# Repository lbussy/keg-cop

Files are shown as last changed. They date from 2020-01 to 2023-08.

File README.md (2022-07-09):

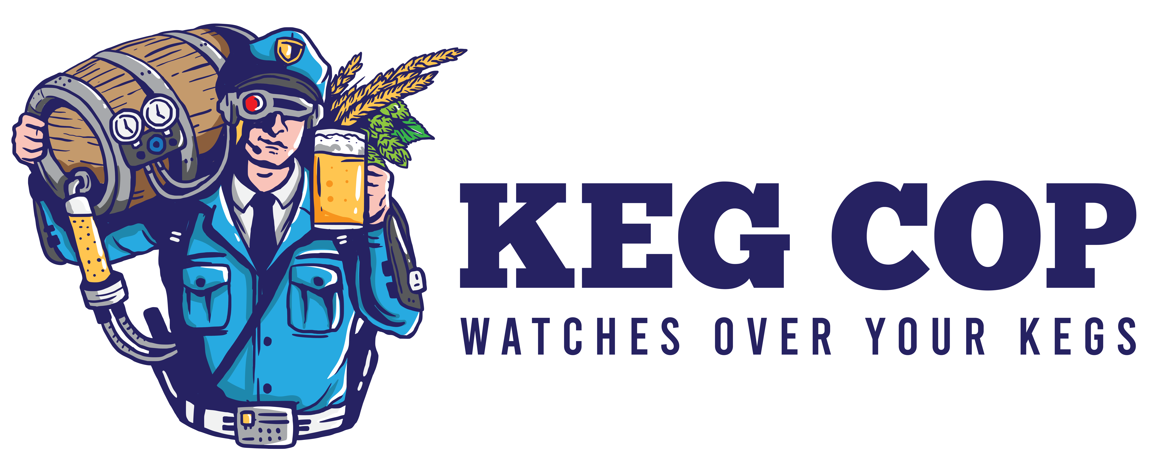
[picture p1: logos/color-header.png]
Keg Cop Logo
 

# Keg Cop

*Beverage Lines, Monitored.*

Keg Cop is an inexpensive and, most of all, simple to operate WiFi-enabled solution to maintain information about your Keezer, Kegerator, and Kegs.  Keg Cop enables you to use flowmeters of your choice (Swissflow during development) to monitor the contents of your kegs, and it even has a built-in Web UI to display what is on tap and how much is left.

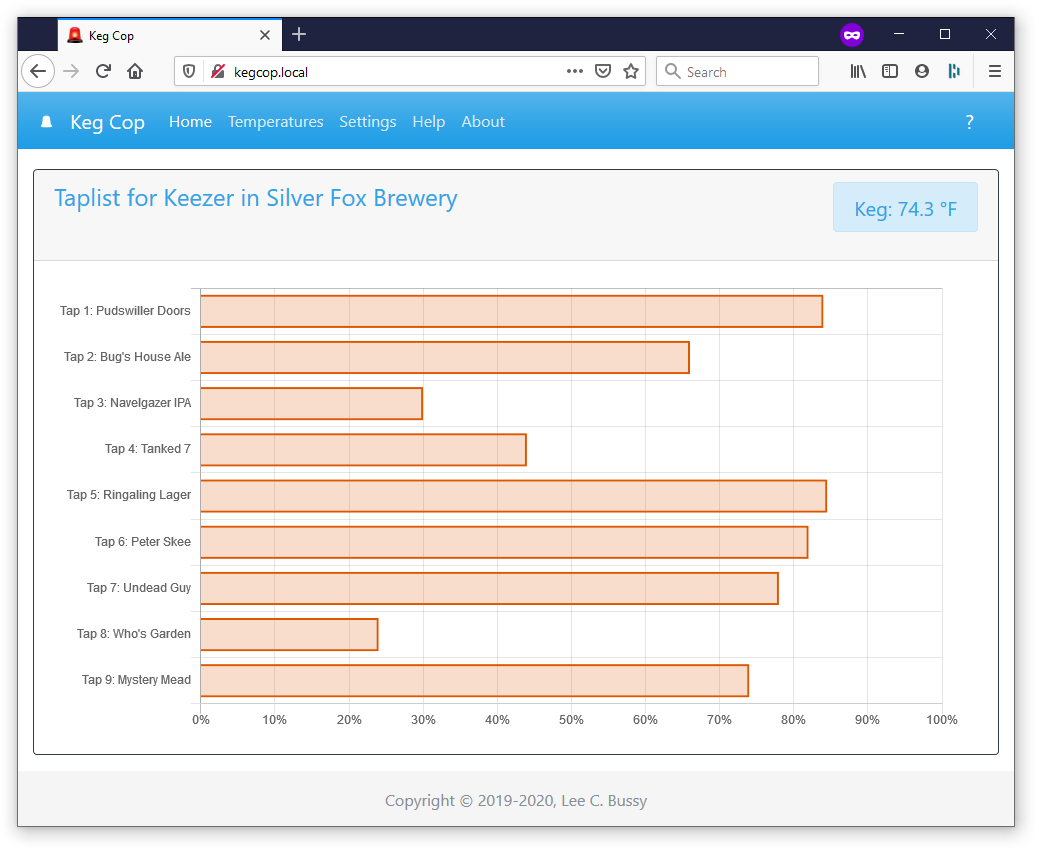
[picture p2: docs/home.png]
Keg Cop Index

 
Keg Cop uses an inexpensive ESP32 controller to control and monitor all aspects of your beverage dispensing solution.  If you already have flowmeters from another project, you can easily use those and upgrade your approach.  It will support one to nine flowmeters, and it will even control your temperatures for you.

You may employ up to five different temperature sensors to show you things like tower temp, keg temp, top and bottom of your Keezer, and you can even monitor the room temperature.

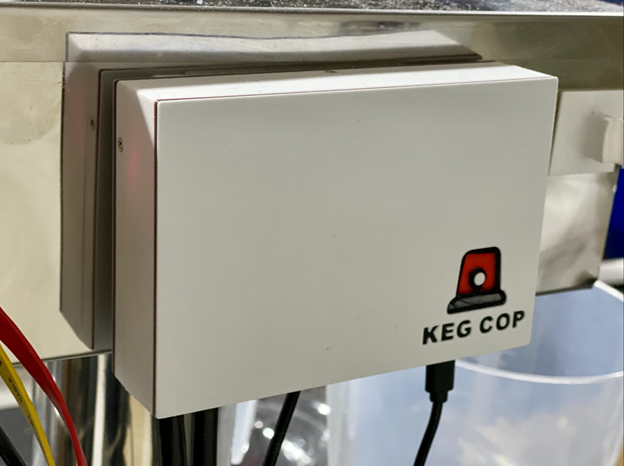
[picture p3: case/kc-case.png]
Keg Cop Case

 
I designed this project as a complete system from the ground up.  Everything is provided, including board files for PCBs and 3D models for cases.  I’m releasing this system as something which provides either a complete recipe for success or enough information to allow you to roll your own if that’s your thing.

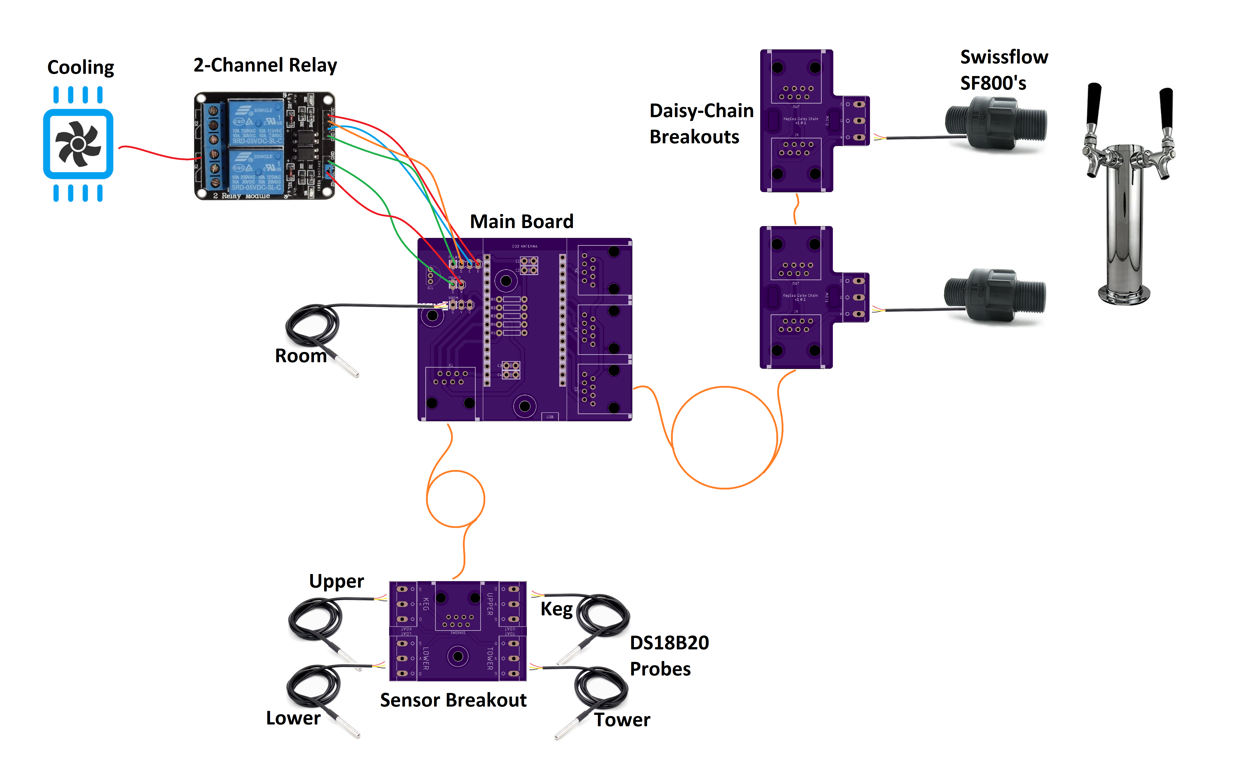
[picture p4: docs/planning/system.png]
Keg Cop System


Whether you have one flowmeter or nine, Keg Cop can handle them.  Have more?  Add another controller, and KegScreen (coming soon!) will seamlessly display them all.

Want even more capabilities?  Keg Cop will report pours to Raspberry Pints via MQTT or a web endpoint with a generic JSON packet.
Still not enough?  Keg Cop was designed alongside KegScreen to work hand in hand with this exciting upcoming full-featured tap list solution.

Full documentation is provided, including the API and hardware assembly.  Or, if you are a more nuts and bolts person, GitHub may be the place for you!

Links and Support:

-	Home Page
-	Project on GitHub
-	Documentation
-	Report an Issue or Bug
-	Get support or chat with other users

This release has been a long time coming, and I’m excited to share this with you.  I want to thank the following folks from Homebrewtalk who have contributed in one way or another:

-	@thorrak
-	@gromitdj
-	@UncleD
-	@day_trippr
-	@cripplecreek

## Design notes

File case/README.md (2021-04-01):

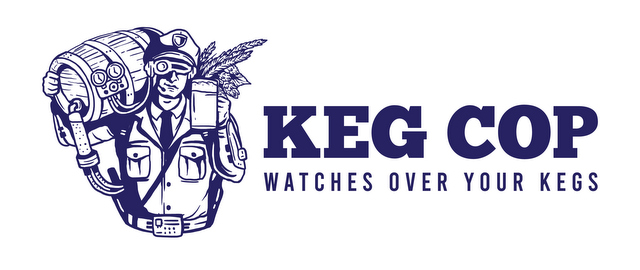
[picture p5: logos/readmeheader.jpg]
Keg Cop Logo Keg Cop (http://www.kegcop.com/)


# 3D Printed Cases

Within these folders are 3D models of cases which you may use in your own deployments:

- **Main Boards:**  Contains the top and bottom case halves for the main board.  These have been tested in PLA and PETG.  Additionally, there is a color-print enabled logo in the lid should you choose to take advantage of it.  I recommend the following layers:
    - 0.15mm layers
        - 0.00 - 0.65: Main body color (I used white)
        - 0.80 - 1.25: Dark border color (I used black)
        - 1.40 - 1.85: Base color (I used silver)
        - 2.00 - 2.60: Globe color (I used translucent red)
    - 0.20mm layers
        - 0.00 - 0.60: Main body color (I used white)
        - 0.80 - 1.20: Dark border color (I used black)
        - 1.40 - 1.80: Base color (I used silver)
        - 2.00 - 2.60: Globe color (I used translucent red)

Layer Configuration

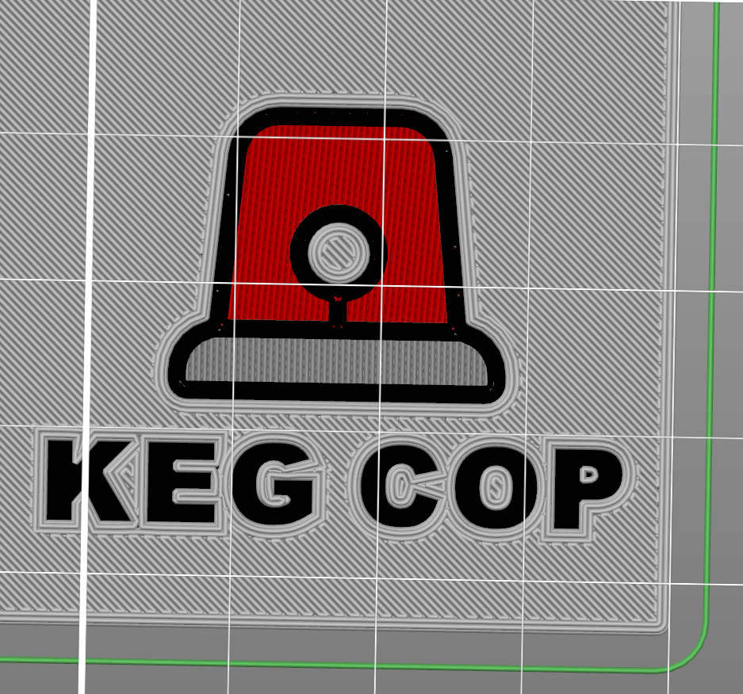
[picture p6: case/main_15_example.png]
Layer Render


- **Breakouts:**
    - Daisy Chain:
    - Temp Sensor:

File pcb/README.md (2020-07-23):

Keg Cop Logo Keg Cop (http://www.kegcop.com/)

# Printed Circuit Boards for Keg Cop

Contained here are two folders:

- **Main Boards:** Boards which receive the D32 controller, and provide connectivity to the breakouts.
- **Breakouts:** Boards which distribute and receive signals within the kegerator/keezer.

The type and number required of each board will vary by the intended configuration.  Use [the documentation](https://docs.kegcop.com) to determine which boards you need and how many:

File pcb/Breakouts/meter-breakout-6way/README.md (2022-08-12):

# Six-way Meter Breakout PCB

This PCB interfaces between the main Keg Cop board and up to six flow meters, which will connect via board-mounted JST-XH connectors.  This PCB is not designed to daisy-chain.

## Design info
This PCB was designed using [KiCad 6.0](https://www.kicad.org/), a free and open-source, cross-platform electronics design suite.  Design files are provided if you'd like to make changes to the design.  Otherwise, you can download the .zip file from the `Gerber` directory and upload to your PCB fab of choice.

## Board images
Front:
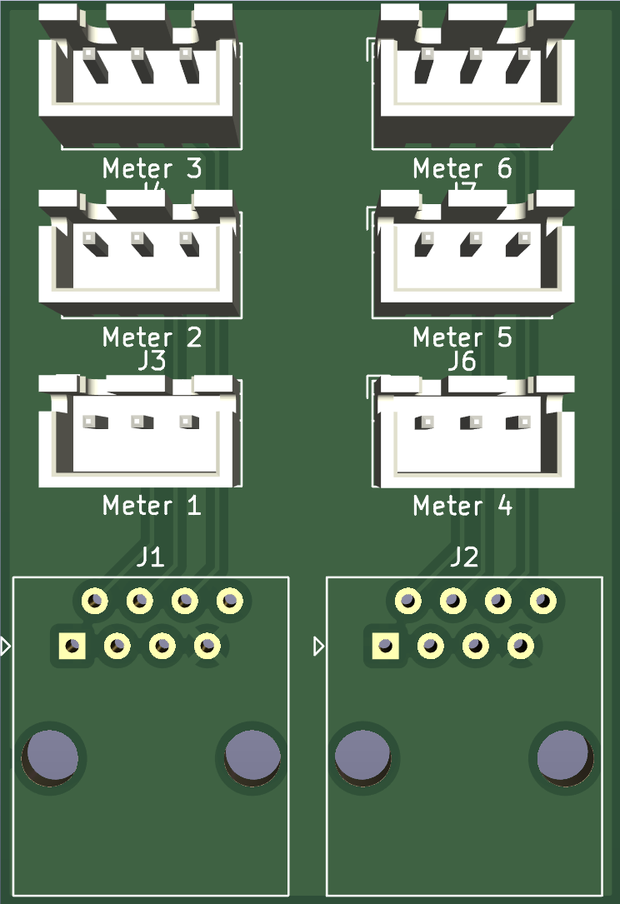
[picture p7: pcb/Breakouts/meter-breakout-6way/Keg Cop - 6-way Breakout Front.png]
Front PCB Rendering


Back:
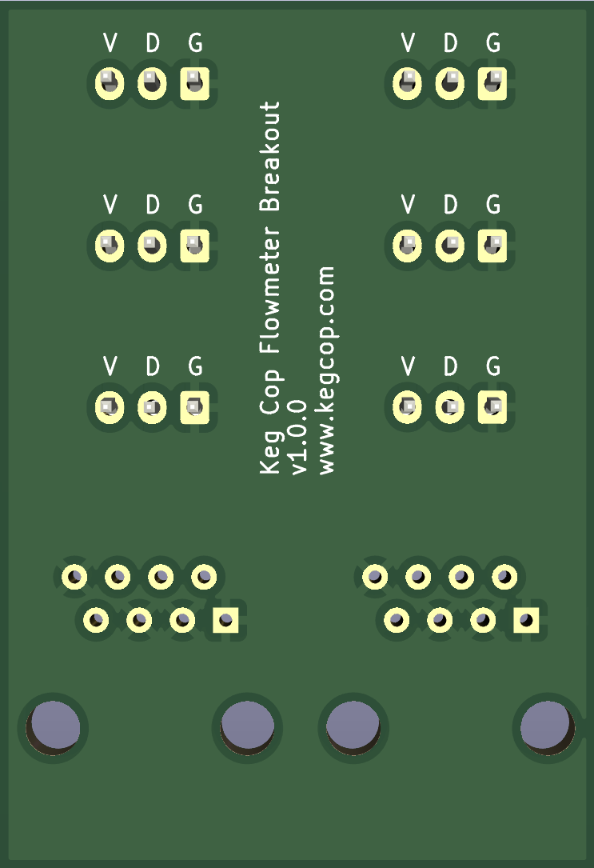
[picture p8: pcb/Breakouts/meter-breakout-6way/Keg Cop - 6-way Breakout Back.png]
Back PCB Rendering


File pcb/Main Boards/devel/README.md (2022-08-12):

# Development Board

It is exceedingly unlikely that anyone but me will need this PCB.

I designed this to allow me a physical interface into the software for development work.  This provides pushbuttons for emulating flowmeters, and a few DS18B20's for temperature values.

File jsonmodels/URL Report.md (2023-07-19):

Generic REST Report JSON Model:
================================

JSON Definition:
----------------

```
{
    "api":"xxxxxxxxxxxxxxxxxxxxxxxxxxxxxxxx",
	"guid":"xxxxxxxx",
    "hostname":"xxxxxxxxxxxxxxxxxxxxxxxxxxxxxxxx",
    "breweryname":"xxxxxxxxxxxxxxxxxxxxxxxxxxxxxxxxxxxxxxxxxxxxxxxxxxxxxxxxxxxxxxxx",
    "kegeratorname":"xxxxxxxxxxxxxxxxxxxxxxxxxxxxxxxxxxxxxxxxxxxxxxxxxxxxxxxxxxxxxxxx",
    "reporttype":"xxxxxxxxxxxxxxxx",
    "imperial": false,
	"coolonhigh": true,
    "controlpoint": 99,
    "setpoint": 999.999,
    "state": 99,
    "controlenabled": false,
	"tfancontrolenabled": false,
	"tfansetpoint": 100,
	"tfanstate": 99,
	"tfanonhigh": false,
    "sensors": [
        {
            "name": "xxxxxxxxxxxxxxxxxxxxxxxxxxxxxxxx",
            "enable": false,
            "value": 999.999
        },
        {
            "name": "xxxxxxxxxxxxxxxxxxxxxxxxxxxxxxxx",
            "enable": false,
            "value": 999.999
        },
        {
            "name": "xxxxxxxxxxxxxxxxxxxxxxxxxxxxxxxx",
            "enable": false,
            "value": 999.999
        },
        {
            "name": "xxxxxxxxxxxxxxxxxxxxxxxxxxxxxxxx",
            "enable": false,
            "value": 999.999
        },
        {
            "name": "xxxxxxxxxxxxxxxxxxxxxxxxxxxxxxxx",
            "enable": false,
            "value": 999.999
        }
    ],
	"taps": [
        {
			"tapid": 99,
			"ppu": 999999,
			"name": "xxxxxxxxxxxxxxxxxxxxxxxxxxxxxxxxxxxxxxxxxxxxxxxxxxxxxxxxxxxxxxxx",
			"capacity": 999.9999,
			"remaining": 999.9999,
			"active": false
		},
		{
			"tapid": 99,
			"ppu": 999999,
			"name": "xxxxxxxxxxxxxxxxxxxxxxxxxxxxxxxxxxxxxxxxxxxxxxxxxxxxxxxxxxxxxxxx",
			"capacity": 999.9999,
			"remaining": 999.9999,
			"active": false
		},
		{
			"tapid": 99,
			"ppu": 999999,
			"name": "xxxxxxxxxxxxxxxxxxxxxxxxxxxxxxxxxxxxxxxxxxxxxxxxxxxxxxxxxxxxxxxx",
			"capacity": 999.9999,
			"remaining": 999.9999,
			"active": false
		},
		{
			"tapid": 99,
			"ppu": 999999,
			"name": "xxxxxxxxxxxxxxxxxxxxxxxxxxxxxxxxxxxxxxxxxxxxxxxxxxxxxxxxxxxxxxxx",
			"capacity": 999.9999,
			"remaining": 999.9999,
			"active": false
		},
		{
			"tapid": 99,
			"ppu": 999999,
			"name": "xxxxxxxxxxxxxxxxxxxxxxxxxxxxxxxxxxxxxxxxxxxxxxxxxxxxxxxxxxxxxxxx",
			"capacity": 999.9999,
			"remaining": 999.9999,
			"active": false
		},
		{
			"tapid": 99,
			"ppu": 999999,
			"name": "xxxxxxxxxxxxxxxxxxxxxxxxxxxxxxxxxxxxxxxxxxxxxxxxxxxxxxxxxxxxxxxx",
			"capacity": 999.9999,
			"remaining": 999.9999,
			"active": false
		},
		{
			"tapid": 99,
			"ppu": 999999,
			"name": "xxxxxxxxxxxxxxxxxxxxxxxxxxxxxxxxxxxxxxxxxxxxxxxxxxxxxxxxxxxxxxxx",
			"capacity": 999.9999,
			"remaining": 999.9999,
			"active": false
		},
		{
			"tapid": 99,
			"ppu": 999999,
			"name": "xxxxxxxxxxxxxxxxxxxxxxxxxxxxxxxxxxxxxxxxxxxxxxxxxxxxxxxxxxxxxxxx",
			"capacity": 999.9999,
			"remaining": 999.9999,
			"active": false
		},
		{
			"tapid": 99,
			"ppu": 999999,
			"name": "xxxxxxxxxxxxxxxxxxxxxxxxxxxxxxxxxxxxxxxxxxxxxxxxxxxxxxxxxxxxxxxx",
			"capacity": 999.9999,
			"remaining": 999.9999,
			"active": false
		}
	]
}
```

Size:
-----

```
Serialize:  3072
Deserialize:  3072
```

Deserializing / Parsing / Loading:
----------------------------------

```
// Stream& input;

StaticJsonDocument<3072> doc;

DeserializationError error = deserializeJson(doc, input);

if (error) {
  Serial.print("deserializeJson() failed: ");
  Serial.println(error.c_str());
  return;
}

const char* api = doc["api"]; // "xxxxxxxxxxxxxxxxxxxxxxxxxxxxxxxx"
const char* guid = doc["guid"]; // "xxxxxxxx"
const char* hostname = doc["hostname"]; // "xxxxxxxxxxxxxxxxxxxxxxxxxxxxxxxx"
const char* breweryname = doc["breweryname"];
const char* kegeratorname = doc["kegeratorname"];
const char* reporttype = doc["reporttype"]; // "xxxxxxxxxxxxxxxx"
bool imperial = doc["imperial"]; // false
bool coolonhigh = doc["coolonhigh"]; // true
int controlpoint = doc["controlpoint"]; // 99
float setpoint = doc["setpoint"]; // 999.999
int state = doc["state"]; // 99
bool controlenabled = doc["controlenabled"]; // false
bool tfancontrolenabled = doc["tfancontrolenabled"]; // false
int tfansetpoint = doc["tfansetpoint"]; // 100

for (JsonObject sensor : doc["sensors"].as<JsonArray>()) {

  const char* sensor_name = sensor["name"]; // "xxxxxxxxxxxxxxxxxxxxxxxxxxxxxxxx", ...
  bool sensor_enable = sensor["enable"]; // false, false, false, false, false
  float sensor_value = sensor["value"]; // 999.999, 999.999, 999.999, 999.999, 999.999

}

for (JsonObject tap : doc["taps"].as<JsonArray>()) {

  int tap_tapid = tap["tapid"]; // 99, 99, 99, 99, 99, 99, 99, 99, 99
  long tap_ppu = tap["ppu"]; // 999999, 999999, 999999, 999999, 999999, 999999, 999999, 999999, 999999
  const char* tap_name = tap["name"];
  float tap_capacity = tap["capacity"]; // 999.9999, 999.9999, 999.9999, 999.9999, 999.9999, 999.9999, ...
  float tap_remaining = tap["remaining"]; // 999.9999, 999.9999, 999.9999, 999.9999, 999.9999, 999.9999, ...
  bool tap_active = tap["active"]; // false, false, false, false, false, false, false, false, false

}
```

Serializing / Saving:
---------------------

```
StaticJsonDocument<3072> doc;

doc["api"] = "xxxxxxxxxxxxxxxxxxxxxxxxxxxxxxxx";
doc["guid"] = "xxxxxxxx";
doc["hostname"] = "xxxxxxxxxxxxxxxxxxxxxxxxxxxxxxxx";
doc["breweryname"] = "xxxxxxxxxxxxxxxxxxxxxxxxxxxxxxxxxxxxxxxxxxxxxxxxxxxxxxxxxxxxxxxx";
doc["kegeratorname"] = "xxxxxxxxxxxxxxxxxxxxxxxxxxxxxxxxxxxxxxxxxxxxxxxxxxxxxxxxxxxxxxxx";
doc["reporttype"] = "xxxxxxxxxxxxxxxx";
doc["imperial"] = false;
doc["coolonhigh"] = true;
doc["controlpoint"] = 99;
doc["setpoint"] = 999.999;
doc["state"] = 99;
doc["controlenabled"] = false;
doc["tfancontrolenabled"] = false;
doc["tfansetpoint"] = 100;

JsonArray sensors = doc.createNestedArray("sensors");

JsonObject sensors_0 = sensors.createNestedObject();
sensors_0["name"] = "xxxxxxxxxxxxxxxxxxxxxxxxxxxxxxxx";
sensors_0["enable"] = false;
sensors_0["value"] = 999.999;

JsonObject sensors_1 = sensors.createNestedObject();
sensors_1["name"] = "xxxxxxxxxxxxxxxxxxxxxxxxxxxxxxxx";
sensors_1["enable"] = false;
sensors_1["value"] = 999.999;

JsonObject sensors_2 = sensors.createNestedObject();
sensors_2["name"] = "xxxxxxxxxxxxxxxxxxxxxxxxxxxxxxxx";
sensors_2["enable"] = false;
sensors_2["value"] = 999.999;

JsonObject sensors_3 = sensors.createNestedObject();
sensors_3["name"] = "xxxxxxxxxxxxxxxxxxxxxxxxxxxxxxxx";
sensors_3["enable"] = false;
sensors_3["value"] = 999.999;

JsonObject sensors_4 = sensors.createNestedObject();
sensors_4["name"] = "xxxxxxxxxxxxxxxxxxxxxxxxxxxxxxxx";
sensors_4["enable"] = false;
sensors_4["value"] = 999.999;

JsonArray taps = doc.createNestedArray("taps");

JsonObject taps_0 = taps.createNestedObject();
taps_0["tapid"] = 99;
taps_0["ppu"] = 999999;
taps_0["name"] = "xxxxxxxxxxxxxxxxxxxxxxxxxxxxxxxxxxxxxxxxxxxxxxxxxxxxxxxxxxxxxxxx";
taps_0["capacity"] = 999.9999;
taps_0["remaining"] = 999.9999;
taps_0["active"] = false;

JsonObject taps_1 = taps.createNestedObject();
taps_1["tapid"] = 99;
taps_1["ppu"] = 999999;
taps_1["name"] = "xxxxxxxxxxxxxxxxxxxxxxxxxxxxxxxxxxxxxxxxxxxxxxxxxxxxxxxxxxxxxxxx";
taps_1["capacity"] = 999.9999;
taps_1["remaining"] = 999.9999;
taps_1["active"] = false;

JsonObject taps_2 = taps.createNestedObject();
taps_2["tapid"] = 99;
taps_2["ppu"] = 999999;
taps_2["name"] = "xxxxxxxxxxxxxxxxxxxxxxxxxxxxxxxxxxxxxxxxxxxxxxxxxxxxxxxxxxxxxxxx";
taps_2["capacity"] = 999.9999;
taps_2["remaining"] = 999.9999;
taps_2["active"] = false;

JsonObject taps_3 = taps.createNestedObject();
taps_3["tapid"] = 99;
taps_3["ppu"] = 999999;
taps_3["name"] = "xxxxxxxxxxxxxxxxxxxxxxxxxxxxxxxxxxxxxxxxxxxxxxxxxxxxxxxxxxxxxxxx";
taps_3["capacity"] = 999.9999;
taps_3["remaining"] = 999.9999;
taps_3["active"] = false;

JsonObject taps_4 = taps.createNestedObject();
taps_4["tapid"] = 99;
taps_4["ppu"] = 999999;
taps_4["name"] = "xxxxxxxxxxxxxxxxxxxxxxxxxxxxxxxxxxxxxxxxxxxxxxxxxxxxxxxxxxxxxxxx";
taps_4["capacity"] = 999.9999;
taps_4["remaining"] = 999.9999;
taps_4["active"] = false;

JsonObject taps_5 = taps.createNestedObject();
taps_5["tapid"] = 99;
taps_5["ppu"] = 999999;
taps_5["name"] = "xxxxxxxxxxxxxxxxxxxxxxxxxxxxxxxxxxxxxxxxxxxxxxxxxxxxxxxxxxxxxxxx";
taps_5["capacity"] = 999.9999;
taps_5["remaining"] = 999.9999;
taps_5["active"] = false;

JsonObject taps_6 = taps.createNestedObject();
taps_6["tapid"] = 99;
taps_6["ppu"] = 999999;
taps_6["name"] = "xxxxxxxxxxxxxxxxxxxxxxxxxxxxxxxxxxxxxxxxxxxxxxxxxxxxxxxxxxxxxxxx";
taps_6["capacity"] = 999.9999;
taps_6["remaining"] = 999.9999;
taps_6["active"] = false;

JsonObject taps_7 = taps.createNestedObject();
taps_7["tapid"] = 99;
taps_7["ppu"] = 999999;
taps_7["name"] = "xxxxxxxxxxxxxxxxxxxxxxxxxxxxxxxxxxxxxxxxxxxxxxxxxxxxxxxxxxxxxxxx";
taps_7["capacity"] = 999.9999;
taps_7["remaining"] = 999.9999;
taps_7["active"] = false;

JsonObject taps_8 = taps.createNestedObject();
taps_8["tapid"] = 99;
taps_8["ppu"] = 999999;
taps_8["name"] = "xxxxxxxxxxxxxxxxxxxxxxxxxxxxxxxxxxxxxxxxxxxxxxxxxxxxxxxxxxxxxxxx";
taps_8["capacity"] = 999.9999;
taps_8["remaining"] = 999.9999;
taps_8["active"] = false;

serializeJson(doc, output);
```

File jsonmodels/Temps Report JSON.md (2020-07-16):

Temps Report (push) JSON Model:
===============================

JSON Definition:
----------------

```
{
    "api":"xxxxxxxxxxxxxxxxxxxxxxxxxxxxxxxx",
    "breweryname":"xxxxxxxxxxxxxxxxxxxxxxxxxxxxxxxxxxxxxxxxxxxxxxxxxxxxxxxxxxxxxxxx",
    "kegeratorname":"xxxxxxxxxxxxxxxxxxxxxxxxxxxxxxxxxxxxxxxxxxxxxxxxxxxxxxxxxxxxxxxx",
    "reporttype":"xxxxxxxxxxxxxxxx",
    "imperial": false,
    "controlpoint": 99,
    "setting": 999.999,
    "status": 99,
    "controlenabled": false,
    "sensors": [
        {
            "name": "xxxxxxxxxxxxxxxxxxxxxxxxxxxxxxxx",
            "enable": false,
            "value": 999.999
        },
        {
            "name": "xxxxxxxxxxxxxxxxxxxxxxxxxxxxxxxx",
            "enable": false,
            "value": 999.999
        },
        {
            "name": "xxxxxxxxxxxxxxxxxxxxxxxxxxxxxxxx",
            "enable": false,
            "value": 999.999
        },
        {
            "name": "xxxxxxxxxxxxxxxxxxxxxxxxxxxxxxxx",
            "enable": false,
            "value": 999.999
        },
        {
            "name": "xxxxxxxxxxxxxxxxxxxxxxxxxxxxxxxx",
            "enable": false,
            "value": 999.999
        }
    ]
}
```

Size:
-----

```
const size_t capacity = JSON_ARRAY_SIZE(5) + 5*JSON_OBJECT_SIZE(3) + JSON_OBJECT_SIZE(10) + 600;
480+536 = 1016
```

Deserializing / Parsing / Loading:
----------------------------------

```
DynamicJsonDocument doc(capacity);

const char* json = "{\"api\":\"xxxxxxxxxxxxxxxxxxxxxxxxxxxxxxxx\",\"breweryname\":\"xxxxxxxxxxxxxxxxxxxxxxxxxxxxxxxxxxxxxxxxxxxxxxxxxxxxxxxxxxxxxxxx\",\"kegeratorname\":\"xxxxxxxxxxxxxxxxxxxxxxxxxxxxxxxxxxxxxxxxxxxxxxxxxxxxxxxxxxxxxxxx\",\"reporttype\":\"xxxxxxxxxxxxxxxx\",\"imperial\":false,\"controlpoint\":99,\"setting\":999.999,\"status\":99,\"controlenabled\":false,\"sensors\":[{\"name\":\"xxxxxxxxxxxxxxxxxxxxxxxxxxxxxxxx\",\"enable\":false,\"value\":999.999},{\"name\":\"xxxxxxxxxxxxxxxxxxxxxxxxxxxxxxxx\",\"enable\":false,\"value\":999.999},{\"name\":\"xxxxxxxxxxxxxxxxxxxxxxxxxxxxxxxx\",\"enable\":false,\"value\":999.999},{\"name\":\"xxxxxxxxxxxxxxxxxxxxxxxxxxxxxxxx\",\"enable\":false,\"value\":999.999},{\"name\":\"xxxxxxxxxxxxxxxxxxxxxxxxxxxxxxxx\",\"enable\":false,\"value\":999.999}]}";

deserializeJson(doc, json);

const char* api = doc["api"]; // "xxxxxxxxxxxxxxxxxxxxxxxxxxxxxxxx"
const char* breweryname = doc["breweryname"]; // "xxxxxxxxxxxxxxxxxxxxxxxxxxxxxxxxxxxxxxxxxxxxxxxxxxxxxxxxxxxxxxxx"
const char* kegeratorname = doc["kegeratorname"]; // "xxxxxxxxxxxxxxxxxxxxxxxxxxxxxxxxxxxxxxxxxxxxxxxxxxxxxxxxxxxxxxxx"
const char* reporttype = doc["reporttype"]; // "xxxxxxxxxxxxxxxx"
bool imperial = doc["imperial"]; // false
int controlpoint = doc["controlpoint"]; // 99
float setting = doc["setting"]; // 999.999
int status = doc["status"]; // 99
bool controlenabled = doc["controlenabled"]; // false

JsonArray sensors = doc["sensors"];

JsonObject sensors_0 = sensors[0];
const char* sensors_0_name = sensors_0["name"]; // "xxxxxxxxxxxxxxxxxxxxxxxxxxxxxxxx"
bool sensors_0_enable = sensors_0["enable"]; // false
float sensors_0_value = sensors_0["value"]; // 999.999

JsonObject sensors_1 = sensors[1];
const char* sensors_1_name = sensors_1["name"]; // "xxxxxxxxxxxxxxxxxxxxxxxxxxxxxxxx"
bool sensors_1_enable = sensors_1["enable"]; // false
float sensors_1_value = sensors_1["value"]; // 999.999

JsonObject sensors_2 = sensors[2];
const char* sensors_2_name = sensors_2["name"]; // "xxxxxxxxxxxxxxxxxxxxxxxxxxxxxxxx"
bool sensors_2_enable = sensors_2["enable"]; // false
float sensors_2_value = sensors_2["value"]; // 999.999

JsonObject sensors_3 = sensors[3];
const char* sensors_3_name = sensors_3["name"]; // "xxxxxxxxxxxxxxxxxxxxxxxxxxxxxxxx"
bool sensors_3_enable = sensors_3["enable"]; // false
float sensors_3_value = sensors_3["value"]; // 999.999

JsonObject sensors_4 = sensors[4];
const char* sensors_4_name = sensors_4["name"]; // "xxxxxxxxxxxxxxxxxxxxxxxxxxxxxxxx"
bool sensors_4_enable = sensors_4["enable"]; // false
float sensors_4_value = sensors_4["value"]; // 999.999
```

Serializing / Saving:
---------------------

```
const size_t capacity = JSON_ARRAY_SIZE(5) + 5*JSON_OBJECT_SIZE(3) + JSON_OBJECT_SIZE(10);
DynamicJsonDocument doc(capacity);

doc["api"] = "xxxxxxxxxxxxxxxxxxxxxxxxxxxxxxxx";
doc["breweryname"] = "xxxxxxxxxxxxxxxxxxxxxxxxxxxxxxxxxxxxxxxxxxxxxxxxxxxxxxxxxxxxxxxx";
doc["kegeratorname"] = "xxxxxxxxxxxxxxxxxxxxxxxxxxxxxxxxxxxxxxxxxxxxxxxxxxxxxxxxxxxxxxxx";
doc["reporttype"] = "xxxxxxxxxxxxxxxx";
doc["imperial"] = false;
doc["controlpoint"] = 99;
doc["setting"] = 999.999;
doc["status"] = 99;
doc["controlenabled"] = false;

JsonArray sensors = doc.createNestedArray("sensors");

JsonObject sensors_0 = sensors.createNestedObject();
sensors_0["name"] = "xxxxxxxxxxxxxxxxxxxxxxxxxxxxxxxx";
sensors_0["enable"] = false;
sensors_0["value"] = 999.999;

JsonObject sensors_1 = sensors.createNestedObject();
sensors_1["name"] = "xxxxxxxxxxxxxxxxxxxxxxxxxxxxxxxx";
sensors_1["enable"] = false;
sensors_1["value"] = 999.999;

JsonObject sensors_2 = sensors.createNestedObject();
sensors_2["name"] = "xxxxxxxxxxxxxxxxxxxxxxxxxxxxxxxx";
sensors_2["enable"] = false;
sensors_2["value"] = 999.999;

JsonObject sensors_3 = sensors.createNestedObject();
sensors_3["name"] = "xxxxxxxxxxxxxxxxxxxxxxxxxxxxxxxx";
sensors_3["enable"] = false;
sensors_3["value"] = 999.999;

JsonObject sensors_4 = sensors.createNestedObject();
sensors_4["name"] = "xxxxxxxxxxxxxxxxxxxxxxxxxxxxxxxx";
sensors_4["enable"] = false;
sensors_4["value"] = 999.999;

serializeJson(doc, Serial);
```

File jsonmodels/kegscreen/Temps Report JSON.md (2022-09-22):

Temperatures Report JSON Model:
================================

JSON Definition:
----------------

```
{
    "api":"xxxxxxxxxxxxxxxxxxxxxxxxxxxxxxxx",
    "guid":"xxxxxxxx",
    "hostname":"xxxxxxxxxxxxxxxxxxxxxxxxxxxxxxxx",
    "breweryname":"xxxxxxxxxxxxxxxxxxxxxxxxxxxxxxxxxxxxxxxxxxxxxxxxxxxxxxxxxxxxxxxx",
    "kegeratorname":"xxxxxxxxxxxxxxxxxxxxxxxxxxxxxxxxxxxxxxxxxxxxxxxxxxxxxxxxxxxxxxxx",
    "reporttype":"xxxxxxxxxxxxxxxx",
    "imperial": false,
    "coolonhigh": true,
    "controlpoint": 99,
    "setting": 999.999,
    "status": 99,
    "controlenabled": false,
    "tfancontrolenabled": false,
    "tfansetpoint": 100,
    "tfanstate": 99,
    "tfanonhigh": true,

    "sensors": [
        {
            "name": "xxxxxxxxxxxxxxxxxxxxxxxxxxxxxxxx",
            "enable": false,
            "value": 999.999
        },
        {
            "name": "xxxxxxxxxxxxxxxxxxxxxxxxxxxxxxxx",
            "enable": false,
            "value": 999.999
        },
        {
            "name": "xxxxxxxxxxxxxxxxxxxxxxxxxxxxxxxx",
            "enable": false,
            "value": 999.999
        },
        {
            "name": "xxxxxxxxxxxxxxxxxxxxxxxxxxxxxxxx",
            "enable": false,
            "value": 999.999
        },
        {
            "name": "xxxxxxxxxxxxxxxxxxxxxxxxxxxxxxxx",
            "enable": false,
            "value": 999.999
        }
    ]
}
```

Size:
-----

```
Serialize:  1024
Deserialize:  1536
```

Deserializing / Parsing / Loading:
----------------------------------

```
// Stream& input;

StaticJsonDocument<1536> doc;

DeserializationError error = deserializeJson(doc, input);

if (error) {
  Serial.print("deserializeJson() failed: ");
  Serial.println(error.c_str());
  return;
}

const char* api = doc["api"]; // "xxxxxxxxxxxxxxxxxxxxxxxxxxxxxxxx"
const char* guid = doc["guid"]; // "xxxxxxxx"
const char* hostname = doc["hostname"]; // "xxxxxxxxxxxxxxxxxxxxxxxxxxxxxxxx"
const char* breweryname = doc["breweryname"];
const char* kegeratorname = doc["kegeratorname"];
const char* reporttype = doc["reporttype"]; // "xxxxxxxxxxxxxxxx"
bool imperial = doc["imperial"]; // false
bool coolonhigh = doc["coolonhigh"]; // true
int controlpoint = doc["controlpoint"]; // 99
float setting = doc["setting"]; // 999.999
int status = doc["status"]; // 99
bool controlenabled = doc["controlenabled"]; // false
bool tfancontrolenabled = doc["tfancontrolenabled"]; // false
int tfansetpoint = doc["tfansetpoint"]; // 100

for (JsonObject sensor : doc["sensors"].as<JsonArray>()) {

  const char* sensor_name = sensor["name"]; // "xxxxxxxxxxxxxxxxxxxxxxxxxxxxxxxx", ...
  bool sensor_enable = sensor["enable"]; // false, false, false, false, false
  float sensor_value = sensor["value"]; // 999.999, 999.999, 999.999, 999.999, 999.999

}
```

Serializing / Saving:
---------------------

```
StaticJsonDocument<1024> doc;

doc["api"] = "xxxxxxxxxxxxxxxxxxxxxxxxxxxxxxxx";
doc["guid"] = "xxxxxxxx";
doc["hostname"] = "xxxxxxxxxxxxxxxxxxxxxxxxxxxxxxxx";
doc["breweryname"] = "xxxxxxxxxxxxxxxxxxxxxxxxxxxxxxxxxxxxxxxxxxxxxxxxxxxxxxxxxxxxxxxx";
doc["kegeratorname"] = "xxxxxxxxxxxxxxxxxxxxxxxxxxxxxxxxxxxxxxxxxxxxxxxxxxxxxxxxxxxxxxxx";
doc["reporttype"] = "xxxxxxxxxxxxxxxx";
doc["imperial"] = false;
doc["coolonhigh"] = true;
doc["controlpoint"] = 99;
doc["setting"] = 999.999;
doc["status"] = 99;
doc["controlenabled"] = false;
doc["tfancontrolenabled"] = false;
doc["tfansetpoint"] = 100;

JsonArray sensors = doc.createNestedArray("sensors");

JsonObject sensors_0 = sensors.createNestedObject();
sensors_0["name"] = "xxxxxxxxxxxxxxxxxxxxxxxxxxxxxxxx";
sensors_0["enable"] = false;
sensors_0["value"] = 999.999;

JsonObject sensors_1 = sensors.createNestedObject();
sensors_1["name"] = "xxxxxxxxxxxxxxxxxxxxxxxxxxxxxxxx";
sensors_1["enable"] = false;
sensors_1["value"] = 999.999;

JsonObject sensors_2 = sensors.createNestedObject();
sensors_2["name"] = "xxxxxxxxxxxxxxxxxxxxxxxxxxxxxxxx";
sensors_2["enable"] = false;
sensors_2["value"] = 999.999;

JsonObject sensors_3 = sensors.createNestedObject();
sensors_3["name"] = "xxxxxxxxxxxxxxxxxxxxxxxxxxxxxxxx";
sensors_3["enable"] = false;
sensors_3["value"] = 999.999;

JsonObject sensors_4 = sensors.createNestedObject();
sensors_4["name"] = "xxxxxxxxxxxxxxxxxxxxxxxxxxxxxxxx";
sensors_4["enable"] = false;
sensors_4["value"] = 999.999;

serializeJson(doc, output);
```

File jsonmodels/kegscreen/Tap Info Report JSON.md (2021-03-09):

Tap Info Report JSON Model:
===========================

JSON Definition:
----------------

```
{
    "api":"xxxxxxxxxxxxxxxxxxxxxxxxxxxxxxxx",
    "guid":"xxxxxxxx",
    "hostname":"xxxxxxxxxxxxxxxxxxxxxxxxxxxxxxxx",
    "breweryname":"xxxxxxxxxxxxxxxxxxxxxxxxxxxxxxxxxxxxxxxxxxxxxxxxxxxxxxxxxxxxxxxx",
    "kegeratorname":"xxxxxxxxxxxxxxxxxxxxxxxxxxxxxxxxxxxxxxxxxxxxxxxxxxxxxxxxxxxxxxxx",
    "reporttype":"xxxxxxxxxxxxxxxx",
    "imperial":false,
    "tapid":99,
    "name":"xxxxxxxxxxxxxxxxxxxxxxxxxxxxxxxx",
    "ppu":999999,
    "remaining":999.9999,
    "capacity":999.9999,
    "active":false,
    "calibrating":false
}
```

Size:
-----

```
256 or 512
```

Deserializing / Parsing / Loading:
----------------------------------

```
// char* input;
// size_t inputLength; (optional)

StaticJsonDocument<256> doc;

DeserializationError error = deserializeJson(doc, input, inputLength);

if (error) {
  Serial.print(F("deserializeJson() failed: "));
  Serial.println(error.f_str());
  return;
}

const char* api = doc["api"]; // "xxxxxxxxxxxxxxxxxxxxxxxxxxxxxxxx"
const char* guid = doc["guid"]; // "xxxxxxxx"
const char* hostname = doc["hostname"]; // "xxxxxxxxxxxxxxxxxxxxxxxxxxxxxxxx"
const char* breweryname = doc["breweryname"];
const char* kegeratorname = doc["kegeratorname"];
const char* reporttype = doc["reporttype"]; // "xxxxxxxxxxxxxxxx"
bool imperial = doc["imperial"]; // false
int tapid = doc["tapid"]; // 99
const char* name = doc["name"]; // "xxxxxxxxxxxxxxxxxxxxxxxxxxxxxxxx"
long ppu = doc["ppu"]; // 999999
float remaining = doc["remaining"]; // 999.9999
float capacity = doc["capacity"]; // 999.9999
bool active = doc["active"]; // false
bool calibrating = doc["calibrating"]; // false
```

Serializing / Saving:
---------------------

```
StaticJsonDocument<512> doc;

doc["api"] = "xxxxxxxxxxxxxxxxxxxxxxxxxxxxxxxx";
doc["guid"] = "xxxxxxxx";
doc["hostname"] = "xxxxxxxxxxxxxxxxxxxxxxxxxxxxxxxx";
doc["breweryname"] = "xxxxxxxxxxxxxxxxxxxxxxxxxxxxxxxxxxxxxxxxxxxxxxxxxxxxxxxxxxxxxxxx";
doc["kegeratorname"] = "xxxxxxxxxxxxxxxxxxxxxxxxxxxxxxxxxxxxxxxxxxxxxxxxxxxxxxxxxxxxxxxx";
doc["reporttype"] = "xxxxxxxxxxxxxxxx";
doc["imperial"] = false;
doc["tapid"] = 99;
doc["name"] = "xxxxxxxxxxxxxxxxxxxxxxxxxxxxxxxx";
doc["ppu"] = 999999;
doc["remaining"] = 999.9999;
doc["capacity"] = 999.9999;
doc["active"] = false;
doc["calibrating"] = false;

serializeJson(doc, output);
```

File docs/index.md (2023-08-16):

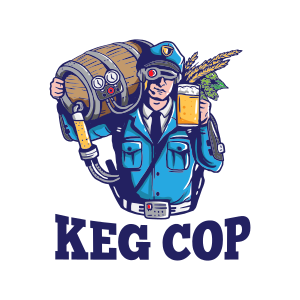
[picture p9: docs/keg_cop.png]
```{image} keg_cop.png
:align: center
:alt: Keg Cop Logo
:scale: 100%
```

# About Keg Cop

We like to brew. Arguably, that means we want to drink. Sure, we can go down to the corner store and buy beer, but that's not in our nature. We spend eight hours brewing to spend a couple of hours enjoying our craft with our friends. Don't try to justify it, or figure out why. It just is.

Invariably, the homebrewer moves from cleaning and filling 24 bottles at a time, to filling one big bottle - a keg.  The problem with that, for all the benefits, is that we cannot quickly tell how much is left.  We can open the keezer and try to guess by lifting it, but that is inaccurate, potentially dangerous, and sometimes impossible.  Keg Cop watches your kegs and tells you exactly how much of your precious brew is left.

```{image} home.png
:align: center
:alt: Keg Cop Home
:scale: 50%
```

At the core, Keg Cop is a small, inexpensive microcontroller far more capable than the computers used for the Apollo moon missions.  You connect the controller to one or more flow meters. Keg Cop makes incredibly precise measurements while you dispense your beer.  The capacity and amount remaining in each display on a compact and mobile responsive web page.  Optionally, you may configure Keg Cop to upload data to several other systems.

Keg Cop is an entirely Free and Open Source offering.  I have provided all source files, including optional 3D printed parts.  You can build this, what follows is the how.

```{toctree}
:caption: 'Table of Contents:'
:glob: true
:maxdepth: 1
:titlesonly: true

planning/index
pcbassembly/index
firmware/index
networking/index
sysassembly/index
operations/index
api/index
troubleshooting/index
context/index
homeassistant/index
contributions/index
todo
```

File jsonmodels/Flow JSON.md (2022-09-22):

Flow Report JSON Model:
=======================

JSON Definition:
----------------

```
{
	"imperial": false,
	"taps": [
        {
			"tapid": 99,
			"label": 99,
			"taplistioTap": 99,
			"pin": 99,
			"ppu": 999999,
			"name": "xxxxxxxxxxxxxxxxxxxxxxxxxxxxxxxxxxxxxxxxxxxxxxxxxxxxxxxxxxxxxxxx",
			"capacity": 999.9999,
			"remaining": 999.9999,
			"active": false,
			"calibrating": false
		},
		{
			"tapid": 99,
			"label": 99,
			"taplistioTap": 99,
			"pin": 99,
			"ppu": 999999,
			"name": "xxxxxxxxxxxxxxxxxxxxxxxxxxxxxxxxxxxxxxxxxxxxxxxxxxxxxxxxxxxxxxxx",
			"capacity": 999.9999,
			"remaining": 999.9999,
			"active": false,
			"calibrating": false
		},
		{
			"tapid": 99,
			"label": 99,
			"taplistioTap": 99,
			"pin": 99,
			"ppu": 999999,
			"name": "xxxxxxxxxxxxxxxxxxxxxxxxxxxxxxxxxxxxxxxxxxxxxxxxxxxxxxxxxxxxxxxx",
			"capacity": 999.9999,
			"remaining": 999.9999,
			"active": false,
			"calibrating": false
		},
		{
			"tapid": 99,
			"label": 99,
			"taplistioTap": 99,
			"pin": 99,
			"ppu": 999999,
			"name": "xxxxxxxxxxxxxxxxxxxxxxxxxxxxxxxxxxxxxxxxxxxxxxxxxxxxxxxxxxxxxxxx",
			"capacity": 999.9999,
			"remaining": 999.9999,
			"active": false,
			"calibrating": false
		},
		{
			"tapid": 99,
			"label": 99,
			"taplistioTap": 99,
			"pin": 99,
			"ppu": 999999,
			"name": "xxxxxxxxxxxxxxxxxxxxxxxxxxxxxxxxxxxxxxxxxxxxxxxxxxxxxxxxxxxxxxxx",
			"capacity": 999.9999,
			"remaining": 999.9999,
			"active": false,
			"calibrating": false
		},
		{
			"tapid": 99,
			"label": 99,
			"taplistioTap": 99,
			"pin": 99,
			"ppu": 999999,
			"name": "xxxxxxxxxxxxxxxxxxxxxxxxxxxxxxxxxxxxxxxxxxxxxxxxxxxxxxxxxxxxxxxx",
			"capacity": 999.9999,
			"remaining": 999.9999,
			"active": false,
			"calibrating": false
		},
		{
			"tapid": 99,
			"label": 99,
			"taplistioTap": 99,
			"pin": 99,
			"ppu": 999999,
			"name": "xxxxxxxxxxxxxxxxxxxxxxxxxxxxxxxxxxxxxxxxxxxxxxxxxxxxxxxxxxxxxxxx",
			"capacity": 999.9999,
			"remaining": 999.9999,
			"active": false,
			"calibrating": false
		},
		{
			"tapid": 99,
			"label": 99,
			"taplistioTap": 99,
			"pin": 99,
			"ppu": 999999,
			"name": "xxxxxxxxxxxxxxxxxxxxxxxxxxxxxxxxxxxxxxxxxxxxxxxxxxxxxxxxxxxxxxxx",
			"capacity": 999.9999,
			"remaining": 999.9999,
			"active": false,
			"calibrating": false
		},
		{
			"tapid": 99,
			"label": 99,
			"taplistioTap": 99,
			"pin": 99,
			"ppu": 999999,
			"name": "xxxxxxxxxxxxxxxxxxxxxxxxxxxxxxxxxxxxxxxxxxxxxxxxxxxxxxxxxxxxxxxx",
			"capacity": 999.9999,
			"remaining": 999.9999,
			"active": false,
			"calibrating": false
		}
	]
}
```

Size:
-----

```
Serialize: 3072
Deserialize: 3072
```

Deserializing / Parsing / Loading:
----------------------------------

```
// Stream& input;

StaticJsonDocument<3072> doc;

DeserializationError error = deserializeJson(doc, input);

if (error) {
  Serial.print("deserializeJson() failed: ");
  Serial.println(error.c_str());
  return;
}

bool imperial = doc["imperial"]; // false

for (JsonObject tap : doc["taps"].as<JsonArray>()) {

  int tap_tapid = tap["tapid"]; // 99, 99, 99, 99, 99, 99, 99, 99, 99
  int tap_label = tap["label"]; // 99, 99, 99, 99, 99, 99, 99, 99, 99
  int tap_taplistioTap = tap["taplistioTap"]; // 99, 99, 99, 99, 99, 99, 99, 99, 99
  int tap_pin = tap["pin"]; // 99, 99, 99, 99, 99, 99, 99, 99, 99
  long tap_ppu = tap["ppu"]; // 999999, 999999, 999999, 999999, 999999, 999999, 999999, 999999, 999999
  const char* tap_name = tap["name"];
  float tap_capacity = tap["capacity"]; // 999.9999, 999.9999, 999.9999, 999.9999, 999.9999, 999.9999, ...
  float tap_remaining = tap["remaining"]; // 999.9999, 999.9999, 999.9999, 999.9999, 999.9999, 999.9999, ...
  bool tap_active = tap["active"]; // false, false, false, false, false, false, false, false, false
  bool tap_calibrating = tap["calibrating"]; // false, false, false, false, false, false, false, false, ...

}
```

Serializing / Saving:
---------------------

```
StaticJsonDocument<3072> doc;

doc["imperial"] = false;

JsonArray taps = doc.createNestedArray("taps");

JsonObject taps_0 = taps.createNestedObject();
taps_0["tapid"] = 99;
taps_0["label"] = 99;
taps_0["taplistioTap"] = 99;
taps_0["pin"] = 99;
taps_0["ppu"] = 999999;
taps_0["name"] = "xxxxxxxxxxxxxxxxxxxxxxxxxxxxxxxxxxxxxxxxxxxxxxxxxxxxxxxxxxxxxxxx";
taps_0["capacity"] = 999.9999;
taps_0["remaining"] = 999.9999;
taps_0["active"] = false;
taps_0["calibrating"] = false;

JsonObject taps_1 = taps.createNestedObject();
taps_1["tapid"] = 99;
taps_1["label"] = 99;
taps_1["taplistioTap"] = 99;
taps_1["pin"] = 99;
taps_1["ppu"] = 999999;
taps_1["name"] = "xxxxxxxxxxxxxxxxxxxxxxxxxxxxxxxxxxxxxxxxxxxxxxxxxxxxxxxxxxxxxxxx";
taps_1["capacity"] = 999.9999;
taps_1["remaining"] = 999.9999;
taps_1["active"] = false;
taps_1["calibrating"] = false;

JsonObject taps_2 = taps.createNestedObject();
taps_2["tapid"] = 99;
taps_2["label"] = 99;
taps_2["taplistioTap"] = 99;
taps_2["pin"] = 99;
taps_2["ppu"] = 999999;
taps_2["name"] = "xxxxxxxxxxxxxxxxxxxxxxxxxxxxxxxxxxxxxxxxxxxxxxxxxxxxxxxxxxxxxxxx";
taps_2["capacity"] = 999.9999;
taps_2["remaining"] = 999.9999;
taps_2["active"] = false;
taps_2["calibrating"] = false;

JsonObject taps_3 = taps.createNestedObject();
taps_3["tapid"] = 99;
taps_3["label"] = 99;
taps_3["taplistioTap"] = 99;
taps_3["pin"] = 99;
taps_3["ppu"] = 999999;
taps_3["name"] = "xxxxxxxxxxxxxxxxxxxxxxxxxxxxxxxxxxxxxxxxxxxxxxxxxxxxxxxxxxxxxxxx";
taps_3["capacity"] = 999.9999;
taps_3["remaining"] = 999.9999;
taps_3["active"] = false;
taps_3["calibrating"] = false;

JsonObject taps_4 = taps.createNestedObject();
taps_4["tapid"] = 99;
taps_4["label"] = 99;
taps_4["taplistioTap"] = 99;
taps_4["pin"] = 99;
taps_4["ppu"] = 999999;
taps_4["name"] = "xxxxxxxxxxxxxxxxxxxxxxxxxxxxxxxxxxxxxxxxxxxxxxxxxxxxxxxxxxxxxxxx";
taps_4["capacity"] = 999.9999;
taps_4["remaining"] = 999.9999;
taps_4["active"] = false;
taps_4["calibrating"] = false;

JsonObject taps_5 = taps.createNestedObject();
taps_5["tapid"] = 99;
taps_5["label"] = 99;
taps_5["taplistioTap"] = 99;
taps_5["pin"] = 99;
taps_5["ppu"] = 999999;
taps_5["name"] = "xxxxxxxxxxxxxxxxxxxxxxxxxxxxxxxxxxxxxxxxxxxxxxxxxxxxxxxxxxxxxxxx";
taps_5["capacity"] = 999.9999;
taps_5["remaining"] = 999.9999;
taps_5["active"] = false;
taps_5["calibrating"] = false;

JsonObject taps_6 = taps.createNestedObject();
taps_6["tapid"] = 99;
taps_6["label"] = 99;
taps_6["taplistioTap"] = 99;
taps_6["pin"] = 99;
taps_6["ppu"] = 999999;
taps_6["name"] = "xxxxxxxxxxxxxxxxxxxxxxxxxxxxxxxxxxxxxxxxxxxxxxxxxxxxxxxxxxxxxxxx";
taps_6["capacity"] = 999.9999;
taps_6["remaining"] = 999.9999;
taps_6["active"] = false;
taps_6["calibrating"] = false;

JsonObject taps_7 = taps.createNestedObject();
taps_7["tapid"] = 99;
taps_7["label"] = 99;
taps_7["taplistioTap"] = 99;
taps_7["pin"] = 99;
taps_7["ppu"] = 999999;
taps_7["name"] = "xxxxxxxxxxxxxxxxxxxxxxxxxxxxxxxxxxxxxxxxxxxxxxxxxxxxxxxxxxxxxxxx";
taps_7["capacity"] = 999.9999;
taps_7["remaining"] = 999.9999;
taps_7["active"] = false;
taps_7["calibrating"] = false;

JsonObject taps_8 = taps.createNestedObject();
taps_8["tapid"] = 99;
taps_8["label"] = 99;
taps_8["taplistioTap"] = 99;
taps_8["pin"] = 99;
taps_8["ppu"] = 999999;
taps_8["name"] = "xxxxxxxxxxxxxxxxxxxxxxxxxxxxxxxxxxxxxxxxxxxxxxxxxxxxxxxxxxxxxxxx";
taps_8["capacity"] = 999.9999;
taps_8["remaining"] = 999.9999;
taps_8["active"] = false;
taps_8["calibrating"] = false;

serializeJson(doc, output);
```

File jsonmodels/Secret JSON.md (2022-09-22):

Secret JSON Model:
========================

JSON Definition:
----------------

```
{
    "secret": "A084217800004839"
}
```

Size:
-----

```
Deserialize: 64
Serialize: 48
```

Deserializing / Parsing / Loading:
----------------------------------

```
// Stream& input;

StaticJsonDocument<64> doc;

DeserializationError error = deserializeJson(doc, input);

if (error) {
  Serial.print("deserializeJson() failed: ");
  Serial.println(error.c_str());
  return;
}

const char* secret = doc["secret"]; // "A084217800004839"
```

Serializing / Saving:
---------------------

```
StaticJsonDocument<48> doc;

doc["secret"] = "A084217800004839";

serializeJson(doc, output);
```

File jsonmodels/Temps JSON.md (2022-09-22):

Temps Report JSON Model:
========================

JSON Definition:
----------------

```
{
    "coolonhigh": true,
    "imperial": false,
    "controlpoint": 99,
    "setting": 999.999,
    "status": 99,
    "controlenabled": false,
	"tfancontrolenabled": false,
	"tfansetpoint": 100,
    "tfanstate": 99,
	"tfanonhigh": false,
    "displayenabled": false,
    "sensors": [
    {
        "name": "xxxxxxxxxxxxxxxxxxxxxxxxxxxxxxxx",
        "enable": false,
        "value": 999.999
    },
    {
        "name": "xxxxxxxxxxxxxxxxxxxxxxxxxxxxxxxx",
        "enable": false,
        "value": 999.999
    },
    {
        "name": "xxxxxxxxxxxxxxxxxxxxxxxxxxxxxxxx",
        "enable": false,
        "value": 999.999
    },
    {
        "name": "xxxxxxxxxxxxxxxxxxxxxxxxxxxxxxxx",
        "enable": false,
        "value": 999.999
    },
    {
        "name": "xxxxxxxxxxxxxxxxxxxxxxxxxxxxxxxx",
        "enable": false,
        "value": 999.999
    }
    ]
}
```

Size:
-----

```
Serialize: 768
Deserialize = 1024
```

Deserializing / Parsing / Loading:
----------------------------------

```
// Stream& input;

StaticJsonDocument<1024> doc;

DeserializationError error = deserializeJson(doc, input);

if (error) {
  Serial.print("deserializeJson() failed: ");
  Serial.println(error.c_str());
  return;
}

bool imperial = doc["imperial"]; // false
int controlpoint = doc["controlpoint"]; // 99
float setting = doc["setting"]; // 999.999
int status = doc["status"]; // 99
bool controlenabled = doc["controlenabled"]; // false
bool tfancontrolenabled = doc["tfancontrolenabled"]; // false
int tfansetpoint = doc["tfansetpoint"]; // 100
bool displayenabled = doc["displayenabled"]; // false

for (JsonObject sensor : doc["sensors"].as<JsonArray>()) {

  const char* sensor_name = sensor["name"]; // "xxxxxxxxxxxxxxxxxxxxxxxxxxxxxxxx", ...
  bool sensor_enable = sensor["enable"]; // false, false, false, false, false
  float sensor_value = sensor["value"]; // 999.999, 999.999, 999.999, 999.999, 999.999

}
```

Serializing / Saving:
---------------------

```
StaticJsonDocument<768> doc;

doc["imperial"] = false;
doc["controlpoint"] = 99;
doc["setting"] = 999.999;
doc["status"] = 99;
doc["controlenabled"] = false;
doc["tfancontrolenabled"] = false;
doc["tfansetpoint"] = 100;
doc["displayenabled"] = false;

JsonArray sensors = doc.createNestedArray("sensors");

JsonObject sensors_0 = sensors.createNestedObject();
sensors_0["name"] = "xxxxxxxxxxxxxxxxxxxxxxxxxxxxxxxx";
sensors_0["enable"] = false;
sensors_0["value"] = 999.999;

JsonObject sensors_1 = sensors.createNestedObject();
sensors_1["name"] = "xxxxxxxxxxxxxxxxxxxxxxxxxxxxxxxx";
sensors_1["enable"] = false;
sensors_1["value"] = 999.999;

JsonObject sensors_2 = sensors.createNestedObject();
sensors_2["name"] = "xxxxxxxxxxxxxxxxxxxxxxxxxxxxxxxx";
sensors_2["enable"] = false;
sensors_2["value"] = 999.999;

JsonObject sensors_3 = sensors.createNestedObject();
sensors_3["name"] = "xxxxxxxxxxxxxxxxxxxxxxxxxxxxxxxx";
sensors_3["enable"] = false;
sensors_3["value"] = 999.999;

JsonObject sensors_4 = sensors.createNestedObject();
sensors_4["name"] = "xxxxxxxxxxxxxxxxxxxxxxxxxxxxxxxx";
sensors_4["enable"] = false;
sensors_4["value"] = 999.999;

serializeJson(doc, output);
```

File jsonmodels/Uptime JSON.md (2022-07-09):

Uptime JSON Model:
========================

JSON Definition:
----------------

```
{
    "lastSecondsSinceBoot": 18446744073709551615,
    "lastTimestamp": 18446744073709551615
}
```

Size:
-----

```
Data structures	32	Bytes needed to stores the JSON objects and arrays in memory
Strings	35	Bytes needed to stores the strings in memory
Total (minimum)	67	Minimum capacity for the JsonDocument.
Total (recommended)	96	Including some slack in case the strings change, and rounded to a power of two 
```

Deserializing / Parsing / Loading:
----------------------------------

```
// Stream& input;

StaticJsonDocument<96> doc;

DeserializationError error = deserializeJson(doc, input);

if (error) {
  Serial.print("deserializeJson() failed: ");
  Serial.println(error.c_str());
  return;
}

double lastSecondsSinceBoot = doc["lastSecondsSinceBoot"]; // 18446744073709552000
double lastTimestamp = doc["lastTimestamp"]; // 18446744073709552000
```

Serializing / Saving:
---------------------

```
StaticJsonDocument<32> doc;

doc["lastSecondsSinceBoot"] = 18446744073709552000;
doc["lastTimestamp"] = 18446744073709552000;

serializeJson(doc, output);
```

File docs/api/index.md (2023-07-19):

(api)=

# Keg Cop API

:::{caution}
As of version 1.2.0, all PUT, POST, and action API usage must include an `X-KegCop-Secret` header with a value identical to the controller GUID.

You may obtain the secret by querying the `/api/v1/info/secret` endpoint.

The "secret" is not intended to replace good security practices, and in no way would I ever recommend that you EVER expose this to the Internet or an unprotected network.
:::

Keg Cop uses a combination of API types:

- [Client-Initiated Communication](#client-initiated-communication)
- [Controller-Initiated Communication](#controller-initiated-communication)

## Client-Initiated Communication

Client-initiated communication is initiated from a system other than the controller to retrieve data or execute a data update or state change in the controller.  These communications are broken down into:

- [Action Page Handlers](#action-page-handlers): Pages that access will initiate a change or present a state.
- [Info Page Handlers](#info-page-handlers): Pages accessed to retrieve information about the controller's state and its systems.
- [Configuration Page Handlers](#configuration-page-handlers): Pages intended to provide a means by which you may update the controller and application features.
- [Filesystem Page Handlers](#filesystem-page-handlers): Allow direct manipulation of the files stored and served by the controller.

### Action Page Handlers

These action page handlers exist within the Action Page API tree:

- [Ping](#ping)
- [WiFi Reset](#wifi-reset)
- [Controller Reset](#controller-reset)
- [Online Update](#online-update)
- [Clear Update State](#clear-update-state)
- [Set Calibration Mode](#set-calibration-mode)
- [Clear Calibration Mode](#clear-calibration-mode)

#### Ping

- **Address:**  {file}`/api/v1/ping/`
- **Valid Methods:**  {file}`GET`
- **Data:**  Ignored
- **Response:** {file}`200 Ok`
- **Description:** While not an action per se, this page provides a simple response to semaphore the controller's presence on the network.
- **Error Message:** None

#### WiFi Reset

- **Address:** {file}`/api/v1/action/wifireset/`
- **Valid Methods:** {file}`PUT`
- **Data:** Ignored
- **Response:** {file}`200 Ok`
- **Description:** This endpoint will initiate the erasure of the saved WiFi credentials and a controller restart.  The restart will not be able to retrieve WiFi credentials; this will cause the controller to start a captive portal for configuration.
- **Error Message:** Any method other than {file}`PUT` will result in a {file}`405 Method Not Allowed` error.

#### Controller Reset

- **Address:** {file}`/api/v1/action/reset/`
- **Valid Methods:** {file}`PUT`
- **Data:** Ignored
- **Response:** {file}`200 Ok`
- **Description:** This endpoint will initiate a controller restart without losing data.
- **Error Message:** Any method other than {file}`PUT` will result in a {file}`405 Method Not Allowed` error.

#### Online Update

- **Address:** {file}`/api/v1/action/updatestart/`
- **Valid Methods:** {file}`PUT`
- **Data:** Ignored
- **Response:** {file}`200 Ok`
- **Description:** This endpoint will initiate a controller upgrade attempt using the firmware available at the author's website.  The controller will attempt to update both firmware and the filesystem.  The controller will restart several times during this process.
- **Error Message:** Any method other than {file}`PUT` will result in a {file}`405 Method Not Allowed` error.

#### Clear Update State

- **Address:** {file}`/api/v1/action/clearupdate/`
- **Valid Methods:** {file}`PUT`
- **Data:** Ignored
- **Response:** {file}`200 Ok`
- **Description:** This endpoint will clear the update semaphores that trigger an update attempt initiated on a controller restart.
- **Error Message:** Any method other than {file}`PUT` will result in a {file}`405 Method Not Allowed` error.

#### Set Calibration Mode

- **Address:** {file}`/api/v1/action/setcalmode/`
- **Valid Methods:** {file}`PUT`
- **Data:** Ignored
- **Response:** {file}`200 Ok`
- **Description:** This endpoint will put the controller in calibration mode.  This mode pauses pour calculations to allow users to measure a pour and calculate pulses per unit.  The pulses accumulated will debit upon completion.
- **Error Message:** Any method other than {file}`PUT` will result in a {file}`405 Method Not Allowed` error.

#### Clear Calibration Mode

- **Address:** {file}`/api/v1/action/clearcalmode/`
- **Valid Methods:** {file}`PUT`
- **Data:** Ignored
- **Response:** {file}`200 Ok`
- **Description:** This endpoint will clear the calibration mode and debit any accumulated pulses.
- **Error Message:** Any method other than {file}`PUT` will result in a {file}`405 Method Not Allowed` error.

### Info Page Handlers

These information provider pages exist within the Info API tree:

- [Reset Reason](#reset-reason)
- [Heap Information](#heap-information)
- [Uptime](#uptime)
- [This Version](#this-version)
- [That Version](#that-version)
- [Pulses](#pulses)
- [Sensors](#sensors)
- [Secret](#secret)
- [Theme](#theme)

#### Reset Reason

- **Address:** {file}`/api/v1/info/resetreason/`
- **Valid Methods:** {file}`ANY`
- **Data:** Ignored
- **Description:** Reason for the most reset controller reset.
- **Error Message:** None.
- **Response:**

```json
{
    "r": {
        "reason": "ESP_RST_POWERON",
        "description": "Reset due to power-on event"
    }
}
```

Where:

- `reason` = Any of the [resetReason] enums listed in [resetreasons.cpp].
- `description` = Any of the [resetDescription] enums listed in [resetreasons.cpp].

#### Heap Information

- **Address:** {file}`/api/v1/info/heap/`
- **Valid Methods:** {file}`ANY`
- **Data:** Ignored
- **Description:** Current information about the controller's heap memory.
- **Error Message:** None.
- **Response:**

```json
{
    "h": {
        "free": 224092,
        "max": 48256,
        "frag": 79
    }
}
```

Where:

- `free` = Total free bytes in the heap
- `max` = Size of largest free block in the heap
- `frag` = Approximate fragmentation of the heap

#### Uptime

- **Address:** {file}`/api/v1/info/uptime/`
- **Valid Methods:** {file}`ANY`
- **Data:** Ignored
- **Description:** Elapsed time since the last controller reset.
- **Error Message:** None.
- **Response:**

```json
{
    "u": {
        "days": 0,
        "hours": 1,
        "minutes": 8,
        "seconds": 38,
        "millis": 246
    }
}
```

#### This Version

- **Address:** {file}`/api/v1/info/thisVersion/`
- **Valid Methods:** {file}`ANY`
- **Data:** Ignored
- **Description:** Currently installed application information.
- **Error Message:** None.
- **Response:**

```json
{
    "fw_version": "0.0.1",
    "fs_version": "0.0.1",
    "branch": "update_versions",
    "build": "d5713a3"
}
```

Where:

- `fw_version` = Current firmware version (tag from Git when built)
- `fs_version` = Current filesystem version (tag from Git when built)
- `branch` = Current Git branch
- `build` = Short hash of current Git commit

#### That Version

- **Address:** {file}`/api/v1/info/thatVersion/`
- **Valid Methods:** {file}`ANY`
- **Data:** Ignored
- **Description:** Version of application available for upgrade.
- **Error Message:** None.
- **Response:**

```json
{
    "fw_version": "0.0.1",
    "fs_version": "0.0.1"
}
```

Where:

- `fw_version` = Available firmware version (tag from Git when built)
- `fs_version` = Available filesystem version (tag from Git when built)

#### Pulses

- **Address:** {file}`/api/v1/info/pulses/`
- **Valid Methods:** {file}`ANY`
- **Data:** Ignored
- **Description:** An array representing the current pulse count per flowmeter during calibration.
- **Error Message:** None.
- **Response:**

```json
{
    "pulses": [
        0,
        0,
        0,
        0,
        0,
        0,
        0,
        0,
        0
    ]
}
```

#### Sensors

- **Address:** {file}`/api/v1/info/sensors/`
- **Valid Methods:** {file}`ANY`
- **Data:** Ignored
- **Description:** Information about temperature sensors and control.
- **Error Message:** None.
- **Response:**

```json
{
    "imperial": true,
    "controlpoint": 4,
    "setting": 35,
    "status": 6,
    "controlenabled": true,
    "sensors": [
        {
        "enable": true,
        "name": "Room",
        "value": -196.6
        },
        {
        "enable": true,
        "name": "Tower",
        "value": -196.6
        },
        {
        "enable": true,
        "name": "Upper Chamber",
        "value": -196.6
        },
        {
        "enable": true,
        "name": "Lower Chamber",
        "value": -196.6
        },
        {
        "enable": true,
        "name": "Keg",
        "value": -196.6
        }
    ],
    "displayenabled": true
}
```

Where:

- `imperial` = True for imperial units, false for metric.
- `controlpoint` = Zero-based index representing the current [sensor] by which the system controls temperature.
- `setting` = Temperature setting in current units.
- `status` = Zero-based index representing the current temperature control [state].
- `controlenabled` = Boolean for enabling temperature control.
- `tfansetpoint` = Temperature setting for tower fan in current units.
- `tfanstate` = Zero-based index representing the current tower temperature control [state].
- `tfancontrolenabled` = Boolean for enabling tower temperature control.
- `sensors` = An array of temperature sensors denoting the `name`, `enable` status, and current `value` of each.
- `displayenabled` = Boolean to display temperatures on the web UI or not.

#### Secret

- **Address:** {file}`/api/v1/info/secret/`
- **Valid Methods:** {file}`ANY`
- **Data:** Ignored
- **Description:** Secret used for PUT operations.
- **Error Message:** None.
- **Response:**

```json
{
    "secret": "5C95AB340000D8A7"
}
```

Where:

- `secret` = Hexidecimal string for representing controller GUID.

#### Theme

- **Address:** {file}`/api/v1/info/theme/`
- **Valid Methods:** {file}`ANY`
- **Data:** Ignored
- **Description:** Name of the current Bootswatch theme.
- **Error Message:** None.
- **Response:**

```json
{
  "theme": "cerulean"
}
```

### Configuration Page Handlers

The configuration page API tree allows retrieval of current states or setting conditions and properties via the same endpoint.  Available pages are:

- [Settings](#settings)
- [Taps](#taps)

#### Settings

`GET` and `PUT` are valid methods for this endpoint.

##### GET

- **Address:** {file}`/api/v1/config/settings/`
- **Valid Methods:** {file}`GET`
- **Data:** Ignored
- **Description:** The {file}`GET` method for this endpoint will return the current endpoint configuration.
- **Error Message:** Any method other than {file}`PUT` or {file}`GET` will result in a {file}`405 Method Not Allowed` error.
- **Response:**

```json
{
    "apconfig": {
        "ssid": "kegcop",
        "passphrase": "kegcop21"
    },
    "copconfig": {
        "guid": "952DE6B40000A1A6",
        "hostname": "kegcop",
        "nodrd": false,
        "breweryname": "Silver Fox Brewery",
        "kegeratorname": "Keezer",
        "controlnum": 0,
        "serial": false,
        "imperial": true,
        "tapsolenoid": true,
        "theme": "cerulean",
        "loglevel": 6,
        "telnet": true,
        "loglevel": 6,
        "kickdetect": true
    },
    "ota": {
        "dospiffs1": false,
        "dospiffs2": false,
        "didupdate": false
    },
    "temps": {
        "setpoint": 35,
        "controlpoint": 4,
        "controlenabled": true,
        "tfancontrolenabled": true,
        "tfansetpoint": 38.5,
        "tfanonhigh": false,
        "roomenabled": true,
        "roomcal": 1,
        "towerenabled": true,
        "towercal": 2,
        "upperenabled": true,
        "uppercal": -1,
        "lowerenabled": true,
        "lowercal": -2,
        "kegenabled": true,
        "kegcal": 3
    },
    "kegscreen": {
        "url": "http://mule.local/kegcop/",
        "update": false
    },
    "rpintstarget": {
        "host": "mule.local",
        "port": 1883,
        "username": "",
        "password": "",
        "topic": "kegcop",
        "update": false
    },
    "hatarget": {
        "host": "hasst.local",
        "port": 1883,
        "username": "",
        "password": "",
        "topic": "homeassistant",
        "update": false
    },
    "taplistio": {
        "venue": "taplist-12345",
        "secret":"secret-abcdefghijk",
        "lastsent":1656966278,
        "update":false
    },
    "urltarget": {
        "url": "http://mule.local",
        "freq": 30,
        "update": false
    }
}
```

##### PUT

- **Address:** {file}`/api/v1/config/settings/`
- **Valid Methods:** {file}`PUT`
- **Response:** `200 Ok` on success, `500 Unable to process data` on failure.
- **Description:**  The {file}`PUT` method for this endpoint will allow endpoint configuration.
- **Error Message:** Any method other than {file}`PUT` or {file}`GET` will result in a {file}`405 Method Not Allowed` error.
- **Data:**

The PUT should follow standard form submission data format, with the following items available.  Items not listed are not available for change.  Some names are not the same as they appear in the JSON; the PUT format is flattened but represented below in groups by the JSON stanza.

###### copconfig

- `guid` - Not configurable via settings; this is a calculated/derived value unique to the controller.
- `hostname` - A string representing a valid hostname (without the .local portion) between 3 and 32 characters.
- `breweryname` - A string representing the brewery name, used to logically group multiple controllers and display the web page.
- `kegeratorname` - A string representing the kegerator name, used to identify the controller and displayed within the web page display.
- `controlnum` - A 1-based index of the controller sequence.  The number should be unique in the brewery and will help identify the same tapid across multiple controllers.
- `imperial` - A boolean representing imperial versus metric units to be used by the controller.  Changing this value will result in a conversion of all stored values to the target units.  Multiple toggles could result in accrued rounding errors and some loss of accuracy.
- `tapsolenoid` - A simple control point intended to control a local solenoid by an upstream system or the web UI.
- `theme` - Any pre-configured Bootstrap-compliant theme.
- `loglevel` - Verbosity of log levels, 6 is highest, 0 is no logging.
- `telnet` - Enables or disables the telnet interface.
- `kickdetect` - Enables or disables the "keg is kicked" detection".

###### temps

- `setpoint` - The temperature setpoint in the configured units to which the system will cool the cabinet.  Setpoint is a floating-point number.
- `controlpoint` - A zero-based index indicating the [sensor] by which the system cools.
- `controlenabled` - A boolean turning temperature control on and off.
- `tfansetpoint` = The temperature setpoint for cooling in the configured units to which the system will cool the tower.  The set point is a floating-point number.
- `tfanstate` = Zero-based index representing the current tower temperature control [state].
- `tfancontrolenabled` = Boolean for enabling tower temperature control.
- `enableroom` - Enable the room sensor to be displayed.
- `roomcal` - A signed floating-point number by which the controller will calibrate the room sensor.
- `enabletower` - Enable the tower sensor to be displayed.
- `towercal` - A signed floating-point number by which the controller will calibrate the tower sensor.
- `enableupper` - Enable the upper chamber sensor to be displayed.
- `uppercal` - A signed floating-point number by which the controller will calibrate the upper chamber sensor.
- `enablelower` - Enable the lower chamber sensor to be displayed.
- `lowercal` - A signed floating-point number by which the controller will calibrate the lower chamber sensor.
- `enablekeg` - Enable the keg sensor to be displayed.
- `kegcal` - A signed floating-point number by which the controller will calibrate the keg sensor.

###### kegscreen (url)

- `kegscreen` - The full URL target for the KegScreen system.

###### rpintstarget

- `rpintshost` - The fully-qualified domain name for the Raspberry Pints system's MQTT broker.
- `rpintsport` - The target MQTT port.
- `rpintsusername` - The MQTT user name, blank if not used.
- `rpintspassword` - The MQTT password, blank if not used.
- `rpintstopic` - The MQTT topic.

###### hatarget

- `hahost` - The fully-qualified domain name for the Home Assistant system's MQTT broker.
- `haport` - The target MQTT port.
- `hausername` - The MQTT user name, blank if not used.
- `hapassword` - The MQTT password, blank if not used.
- `hatopic` - The MQTT topic.

###### taplistio

- `venue` - The taplist.io venue name.
- `secret` - The taplist.io API secret key.
- `lastsent` - Time (epoch) the controller sent the last report.  Used for rate limiting.
- `update` - Whether there is a Taplist.io update pending.

###### urltarget

- `targeturl` - The full URL target for the generic URL target.
- `targetfreq` - The frequency at which the controller will push data.

#### Taps

Both `GET` and `PUT` are valid methods for this endpoint.

##### GET

- **Address:** {file}`/api/v1/config/taps/`
- **Valid Methods:** {file}`GET`
- **Data:** Ignored
- **Description:** The {file}`GET` method for this endpoint will return the current endpoint configuration.
- **Error Message:** Any method other than `PUT` or `GET` will result in a `405 Method Not Allowed` error.
- **Response:**

```json
{
    "imperial": true,
    "taps": [
        {
            "tapid": 0,
            "label": 1,
            "taplistioTap": 1,
            "pin": 4,
            "ppu": 21120,
            "name": "Pudswiller Doors",
            "capacity": 5,
            "remaining": 4.2,
            "active": true,
            "calibrating": false
        },
        {
            "tapid": 1,
            "label": 2,
            "taplistioTap": 0,
            "pin": 16,
            "ppu": 21120,
            "name": "Bug's House Ale",
            "capacity": 5,
            "remaining": 3.3,
            "active": true,
            "calibrating": false
        },
        {
            "tapid": 2,
            "label": 3,
            "taplistioTap": 0,
            "pin": 17,
            "ppu": 21120,
            "name": "Navelgazer IPA",
            "capacity": 5,
            "remaining": 1.5,
            "active": true,
            "calibrating": false
        },
        {
            "tapid": 3,
            "label": 4,
            "taplistioTap": 0,
            "pin": 18,
            "ppu": 21120,
            "name": "Tanked 7",
            "capacity": 5,
            "remaining": 2.2,
            "active": true,
            "calibrating": false
        },
        {
            "tapid": 4,
            "label": 5,
            "taplistioTap": 0,
            "pin": 19,
            "ppu": 21120,
            "name": "Ringaling Lager",
            "capacity": 15.5,
            "remaining": 13.1,
            "active": true,
            "calibrating": false
        },
        {
            "tapid": 5,
            "label": 6,
            "taplistioTap": 0,
            "pin": 21,
            "ppu": 21120,
            "name": "Peter Skee",
            "capacity": 5,
            "remaining": 4.1,
            "active": true,
            "calibrating": false
        },
        {
            "tapid": 6,
            "label": 7,
            "taplistioTap": 0,
            "pin": 22,
            "ppu": 21120,
            "name": "Undead Guy",
            "capacity": 5,
            "remaining": 3.9,
            "active": true,
            "calibrating": false
        },
        {
            "tapid": 7,
            "label": 8,
            "taplistioTap": 0,
            "pin": 23,
            "ppu": 21120,
            "name": "Who's Garden",
            "capacity": 5,
            "remaining": 1.2,
            "active": true,
            "calibrating": false
        },
        {
            "tapid": 8,
            "label": 9,
            "taplistioTap": 0,
            "pin": 13,
            "ppu": 21120,
            "name": "Mystery Mead",
            "capacity": 5,
            "remaining": 3.7,
            "active": true,
            "calibrating": false
        }
    ]
}
```

Where:

- `imperial` = True for imperial units, false for metric.
- `taps` = An array with information for each tap configured.

Tap information follows the following format:

- `tapid` = The zero-based index representing the tap number internally.
- `label` = The one-based label representing the tap number externally.
- `taplistioTap` = The one-based label representing the Taplist.io tap number externally.
- `pin` = The microcontroller [pin] defined for the tap.
- `ppu` = The pulses per configured flow unit.
- `name` = The name of the beverage currently on tap.
- `capacity` = The capacity, in current units, of the attached keg.
- `remaining` = The amount remaining, in current units, of the attached keg.
- `active` = Denotes whether the tap is active (displayed).
- `calibrating` = Switch to put the tap in calibration mode.

##### PUT

- **Address:** {file}`/api/v1/config/taps/`
- **Valid Methods:** {file}`PUT`
- **Response:**  `200 Ok` on success, `500 Unable to process data` on failure.
- **Description:** The {file}`PUT` method for this endpoint will allow endpoint configuration.
- **Error Message:** Any method other than {file}`PUT` or {file}`GET` will result in a `405 Method Not Allowed` error.
- **Data:**

The PUT should follow standard form submission data format, with the following items available.  Items not listed are not available for change.  Some names are not the same as they appear in the JSON; the PUT format is flattened but represented below in groups by the JSON stanza.

`imperial` = True for imperial units, false for metric.
`taps` = An array with information for each configured tap.

The tap array follows the following format for each of the nine available taps:

- `tap` = The zero-based index representing the tap number.
- `label` = The one-based label representing the tap number externally.
- `ppu` = The pulses per configured flow unit.
- `bevname` = The name of the beverage currently on tap.
- `cap` = The capacity of the attached keg in floating-point current units.
- `remain` = The amount remaining of the attached keg in floating-point current units.
- `active` = Denotes whether the tap is active (displayed).

### Filesystem Page Handlers

These action page handlers exist within the Action Page API tree:

- [Filesystem Info](#filesystem-info)
- [List Files](#list-files)
- [Download File](#download-file)
- [Delete File](#delete-file)
- [Upload File](#upload-file)

#### Filesystem Info

- **Address:**  {file}`/api/v1/fs/fsinfo/`
- **Valid Methods:**  {file}`GET`
- **Data:**  Ignored
- **Response:** {file}`200 Ok`
- **Description:** This page provides filesystem usage information.
- **Error Message:** None

```json
{
  "f": {
    "free": 211342,
    "used": 263299,
    "total": 474641
  }
}
```

Where:

- `free`= Free space on the filesystem
- `used`= Space used on the filesystem
- `total`= Total filesystem size

#### List Files

- **Address:**  {file}`/api/v1/fs/listfiles/`
- **Valid Methods:**  {file}`GET`
- **Data:**  Ignored
- **Response:** {file}`200 Ok`
- **Description:** This page lists all files in the filesystem with their size in bytes.
- **Error Message:** None

```json
[
  "README.md|263",
  "about.htm.gz|2195",
  "about.js.gz|1609",
  "android-chrome-192x192.png|23775",
  "android-chrome-512x512.png|101113",
  "appconfig.json|1449",
  "apple-touch-icon.png|15957",
  "browserconfig.xml|244",
  "cerulean_aux.css.gz|158",
  "controllerreset.htm.gz|1700",
  "controllerreset.js.gz|870",
  "drd.dat|4",
  "favicon-16x16.png|1425",
  "favicon-32x32.png|2301",
  "favicon.ico|15086",
  "flowconfig.json|2272",
  "fs.htm|9202",
  "fs.js|11950",
  "help.htm.gz|1966",
  "help.js.gz|229",
  "index.htm.gz|2061",
  "index.js.gz|3166",
  "kegcop.css.gz|507",
  "kegcop_post.js.gz|1079",
  "kegcop_pre.js.gz|4523",
  "kstv.json|105",
  "license.htm.gz|2325",
  "license.js.gz|204",
  "mstile-150x150.png|2582",
  "newedit.htm.gz|1812",
  "newedit.js.gz|1941",
  "ota.htm.gz|1762",
  "ota.js.gz|1590",
  "settings.htm.gz|10013",
  "settings.js.gz|7510",
  "site.webmanifest|424",
  "superhero_aux.css.gz|161",
  "temps.htm.gz|2065",
  "temps.js.gz|2626",
  "test.htm.gz|2247",
  "uptime.csv|534",
  "uptime.json|69",
  "version.json|73",
  "wifireset.htm.gz|1695",
  "wifireset.js.gz|709"
]
```

Where:

`README.md|263`= A file named `README.md` with a size of 263 bytes.

#### Download File

- **Address:**  {file}`/api/v1/fs/downloadfile/`
- **Valid Methods:**  {file}`GET`
- **Data:**  URL-encoded query
- **Response:** {file}`200 Ok`
- **Description:** When the controller receives a proper URL encoded request, this endpoint will prompt the browser for a file download.
- **Error Message:** None

Request encoding:

`?name=README.md`= Where `name` is the query tag name followed by `README.md` as the file the controller will send.

#### Delete File

- **Address:**  {file}`/api/v1/fs/deletefile/`
- **Valid Methods:**  {file}`PUT`
- **Response:** {file}`200 Ok`
- **Description:** This page deletes a file on the filesystem.
- **Error Message:** None
- **Data:**

The PUT should follow standard form submission data format, with the following item available.

`name` = Name of the file to be deleted.

#### Upload File

- **Address:**  {file}`/api/v1/fs/uploadfile/`
- **Valid Methods:**  {file}`POST`
- **Response:** {file}`200 Ok`
- **Description:** This page allows uploading a file to the filesystem.
- **Error Message:** None
- **Data:**

The POST is an `XMLHttpRequest()` with the file contained within the `FormData()` object selected by the "file" input control.

## Controller-Initiated Communication

The controller will send communications, when so configured, via WiFi to upstream systems.

- [KegScreen](#kegscreen)
- [Generic REST](#rest)
- [Raspberry Pints](#raspberry-pints)

### KegScreen

Keg Cop sends five different reports to the upstream KegScreen system:

- [Send Tap Information Report](#send-tap-information-report)
- [Send Pulse Report](#send-pulse-report)
- [Send Kick Report](#send-kick-report)
- [Send Cooling State Report](#send-cooling-state-report)
- [Send Temperature Report](#send-temperature-report)

#### Send Tap Information Report

This report is sent to the upstream system whenever the system logs a change to any tap information.  The configuration is as follows:

```json
{
    "api":"Keg Cop",
    "guid": "952DE6B40000A1A6",
    "hostname":"kegcop",
    "breweryname":"Silver Fox Brewery",
    "kegeratorname":"Keezer",
    "reporttype":"tapinfo",
    "imperial":1,
    "tapid":3,
    "name":"Tanked 7",
    "ppu":21118,
    "remaining":2.2,
    "capacity":5,
    "active":true,
    "calibrating":false
}
```

#### Send Pulse Report

Whenever a pour completes, Keg Cop sends a pour report to the KegScreen system.  The format is as follows:

```json
{
    "api":"Keg Cop",
    "guid": "952DE6B40000A1A6",
    "hostname":"kegcop",
    "breweryname":"Silver Fox Brewery",
    "kegeratorname":"Keezer",
    "reporttype":"pourreport",
    "tapid":0,
    "imperial":true,
    "dispensed":0.004451,
    "remaining":4.195549
}
```

#### Send Kick Report

Keg Cop employs an algorithm for detecting a kicked keg.  When the pour volume exceeds a predetermined amount per second, Keg Cop considers that as evidence the keg is blowing foam and will mark the keg inactive.  The system will send a kick report to the KegScreen system.  The format is as follows:

```json
{
    "api":"Keg Cop",
    "guid": "952DE6B40000A1A6",
    "hostname":"kegcop",
    "breweryname":"Silver Fox Brewery",
    "kegeratorname":"Keezer",
    "reporttype":"kickreport",
    "tapid":0
}
```

#### Send Cooling State Report

A state report is triggered for the KegScreen system whenever the cooling state changes.  The format is as follows:

```json
{
    "api":"Keg Cop",
    "guid": "952DE6B40000A1A6",
    "hostname":"kegcop",
    "breweryname":"Silver Fox Brewery",
    "kegeratorname":"Keezer",
    "reporttype":"coolstate",
    "state":3,
    "tfancontrolenabled": true,
    "tfansetpoint": 38.5,
    "tfanonhigh": false
}
```

Where:

- `API` = Intended to be an indicator to the upstream system for the source of information.
- `guid` = A unique identifier for the controller to help differentiate between multiple Keg Cops.
- `hostname` = Current mDNS hostname.
- `brewername` = A name used to group several Keg Cops logically.
- `reporttype` = The type of information to be found in this report.
- `state` = A zero-based index representing the current temperature control [state]
- `tfansetpoint` = Temperature setting for tower fan in current units.
- `tfanstate` = Zero-based index representing the current tower temperature control [state].
- `tfancontrolenabled` = Boolean for enabling tower temperature control.

#### Send Temperature Report

The controller sends a report containing all temperature points to the KegScreen system every minute.  The format is as follows:

```json
{
    "api":"Keg Cop",
    "guid": "952DE6B40000A1A6",
    "hostname":"kegcop",
    "breweryname":"Silver Fox Brewery",
    "kegeratorname":"Keezer",
    "reporttype":"tempreport",
    "imperial":true,
    "controlpoint":4,
    "setting":35,
    "status":3,
    "controlenabled":true,
    "tfancontrolenabled": true,
    "tfansetpoint": 38.5,
    "tfanonhigh": false,
    "sensors":[
        {
            "name":"Room",
            "value":85.1,
            "enabled":true
        },
        {
            "name":"Tower",
            "value":85.1,
            "enabled":true
        },
        {
            "name":"Upper Chamber",
            "value":78.8,
            "enabled":true
        },
        {
            "name":"Lower Chamber",
            "value":75.2,
            "enabled":true
        },
        {
            "name":"Keg",
            "value":84.2,
            "enabled":true
        }
    ]
}
```

### Generic REST

The Generic REST Report provides a holistic system picture of a custom/third-party endpoint.  It is a timer-based POST; a state change does not trigger it.  As with all target system configurations within Keg Cop, it will post to HTTP only.  The format is as follows:

```json
{
    "api":"Keg Cop",
    "guid": "952DE6B40000A1A6",
    "hostname":"kegcop",
    "breweryname":"Silver Fox Brewery",
    "kegeratorname":"Keezer",
    "reporttype":"targeturlreport",
    "imperial":true,
    "controlpoint":4,
    "setting":35,
    "status":2,
    "controlenabled":true,
    "tfancontrolenabled": true,
    "tfansetpoint": 38.5,
    "tfanonhigh": false,
    "sensors":[
        {
            "name":"Room",
            "value":84.1982,
            "enabled":true
        },
        {
            "name":"Tower",
            "value":84.1964,
            "enabled":true
        },
        {
            "name":"Upper Chamber",
            "value":77.0018,
            "enabled":true
        },
        {
            "name":"Lower Chamber",
            "value":73.6286,
            "enabled":true
        },
        {
            "name":"Keg",
            "value":83.2946,
            "enabled":true
        }
    ],
    "taps":[
        {
            "tapid":0,
            "ppu":21118,
            "name":"Pudswiller Doors",
            "capacity":5,
            "remaining":4.1955,
            "active":false
        },
        {
            "tapid":1,
            "ppu":21118,
            "name":"Bug's House Ale",
            "capacity":5,
            "remaining":3.299195,
            "active":true
        },
        {
            "tapid":2,
            "ppu":21118,
            "name":"Navelgazer IPA",
            "capacity":5,
            "remaining":1.499148,
            "active":true
        },
        {
            "tapid":3,
            "ppu":21118,
            "name":"Tanked 7",
            "capacity":5,
            "remaining":2.197301,
            "active":true
        },
        {
            "tapid":4,
            "ppu":21118,
            "name":"Ringaling Lager",
            "capacity":15.5,
            "remaining":13.09872,
            "active":true
        },
        {
            "tapid":5,
            "ppu":21118,
            "name":"Peter Skee",
            "capacity":5,
            "remaining":4.1,
            "active":true
        },
        {
            "tapid":6,
            "ppu":21118,
            "name":"Undead Guy",
            "capacity":5,
            "remaining":3.899053,
            "active":true
        },
        {
            "tapid":7,
            "ppu":21118,
            "name":"Who's Garden",
            "capacity":5,
            "remaining":1.2,
            "active":true
        }
    ]
}
```

### Raspberry Pints

Keg Cop will send a message via MQTT to a configured endpoint.  Raspberry Pints does not leverage the standard MQTT format; this format is specific to Raspberry Pints.  The structure is as follows:

```
P;-1;0;737
```

Where:

- `P` = A pulse report (the only one currently supported via MQTT by Raspberry Pints.)
- `-1` = The user.  Since Keg Cop does not support user IDs, a -1 indicates "no user."
- `0` = Tap number.
- `737` = Number of raw pulses to report.

[pin]: https://github.com/lbussy/keg-cop/blob/d5713a3323ff9998a7986f801d07a92093c0c3f8/src/config.h#L615-L703
[resetdescription]: https://github.com/lbussy/keg-cop/blob/d5713a3323ff9998a7986f801d07a92093c0c3f8/src/resetreasons.cpp#L41-L53
[resetreason]: https://github.com/lbussy/keg-cop/blob/d5713a3323ff9998a7986f801d07a92093c0c3f8/src/resetreasons.cpp#L27-L39
[resetreasons.cpp]: https://github.com/lbussy/keg-cop/blob/main/src/resetreasons.cpp#L1
[sensor]: https://github.com/lbussy/keg-cop/blob/d5713a3323ff9998a7986f801d07a92093c0c3f8/src/tempsensors.cpp#L25
[state]: https://github.com/lbussy/keg-cop/blob/d5713a3323ff9998a7986f801d07a92093c0c3f8/src/thermostat.h#L31-L41

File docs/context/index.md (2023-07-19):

(context)=

# Context Help

The following are links to context help for the web pages controlling the Keg Cop application.  Generally these are accessed via a hotlink in the web UI.

```{toctree}
:glob: true
:maxdepth: 1
:titlesonly: true

home/index
temperatures/index
settings/controller/index
settings/taps/index
settings/temperature/control/index
settings/temperature/sensors/index
settings/targets/kegscreen/index
settings/targets/rest/index
settings/targets/rpints/index
settings/targets/hass/index
settings/targets/taplistio/index
settings/advanced/calibrate/index
settings/advanced/debug/index
settings/advanced/reset/index
settings/advanced/update/index
settings/advanced/wifi/index
filesystem/index
help/index
about/index
about/license
```

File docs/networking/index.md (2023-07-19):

(networking)=

# Set Up Networking

After flashing the firmware for the first time or erasing network settings, your controller will not participate in any WiFi networks. It starts in what is called "Access Point (AP) Mode," where it serves as a sort of stand-alone wireless network. The onboard LED will flash at 0.5Hz, or one second on, one second off.

## Initial Network Settings

You may use any wireless-capable device to connect to the access point. However, you may achieve the best results using a mobile device. In the following examples, I use an iPhone; however, any device should be very similar. Be aware that using the same machine to follow these instructions may result in the instructions not being available when you connect to the Keg Cop AP. No Internet will be available to your phone or laptop while you go through the process.

In your device settings, search for an available access point named "kegcop."

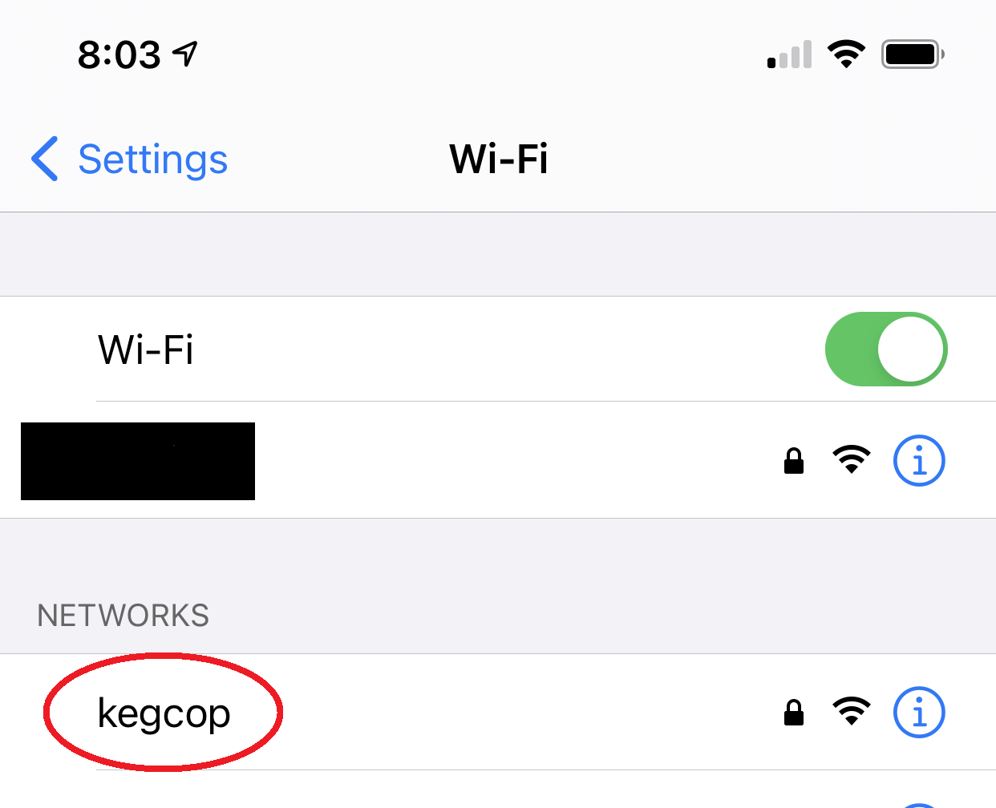
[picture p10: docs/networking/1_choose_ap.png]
```{image} 1_choose_ap.png
:align: center
:alt: Search Access Points
:scale: 25%
```

Connect to the "kegcop" network, and when prompted, enter the password "kegcop21."

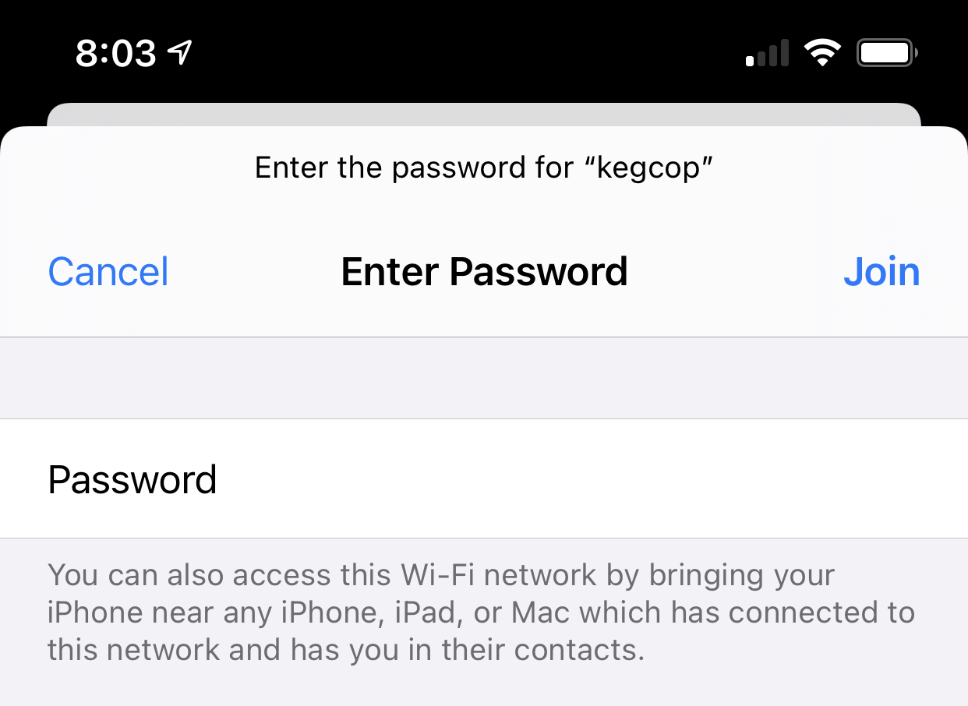
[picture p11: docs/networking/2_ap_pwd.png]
```{image} 2_ap_pwd.png
:align: center
:alt: Enter AP Password
:scale: 25%
```

Your device should connect and briefly show that connection before proceeding.

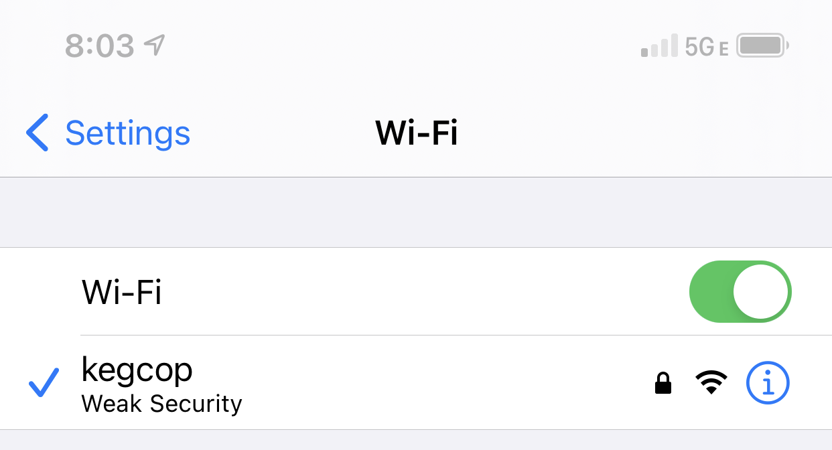
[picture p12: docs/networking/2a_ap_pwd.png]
```{image} 2a_ap_pwd.png
:align: center
:alt: Enter AP Password
:scale: 25%
```

When you connect to the Keg Cop AP, your mobile device or computer should detect it as a "captive portal." Any DNS queries made will always return the AP's IP address, similar to using free WiFi at a restaurant. Your device or computer should open a web browser and connect to the captive portal. If not, open a web browser and connect to the IP address 192.168.4.1.

The captive portal will show, allowing you to continue.

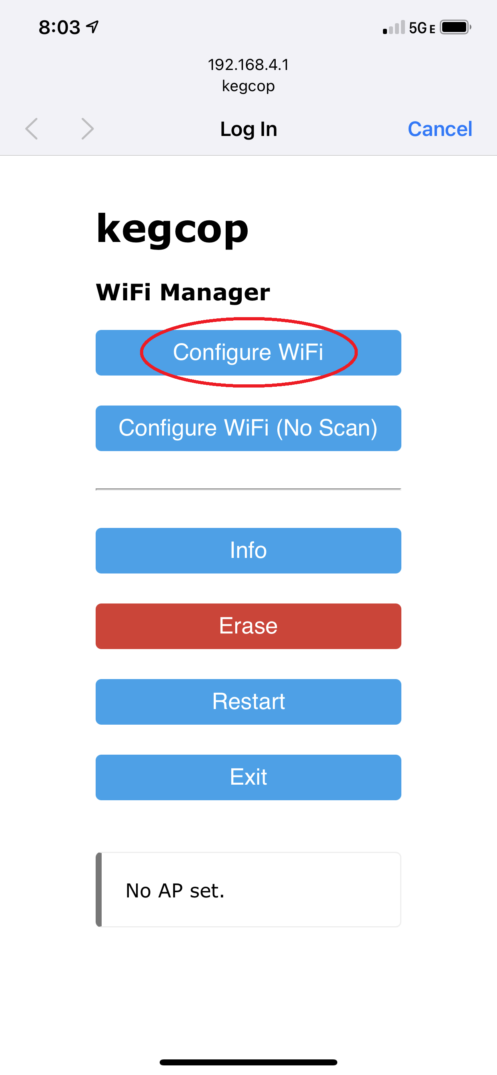
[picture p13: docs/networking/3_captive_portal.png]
```{image} 3_captive_portal.png
:align: center
:alt: Captive Portal
:scale: 20%
```

On the portal page, select "Configure WiFi" to continue.

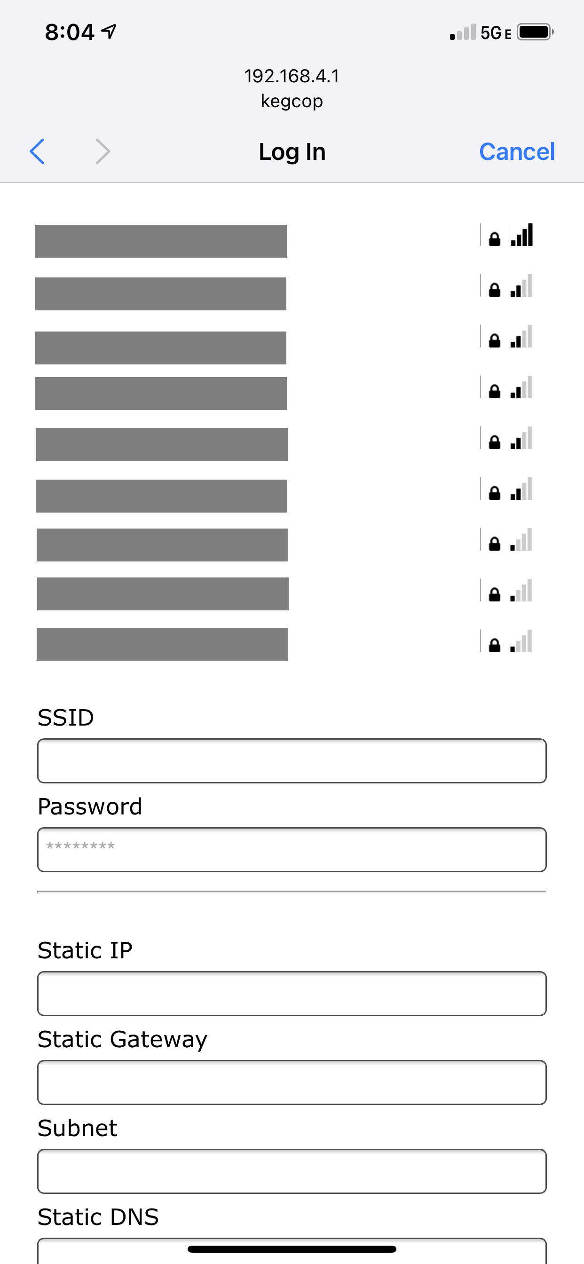
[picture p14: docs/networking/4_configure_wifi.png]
```{image} 4_configure_wifi.png
:align: center
:alt: Configure WiFi
:scale: 20%
```

You should see a list of nearby wireless networks. Select your WiFi network, and the SSID of the network will populate the SSID field. Next, enter your WiFi password. You may also perform a static IP configuration on this page. Such a setup should be used only by those who understand the implications and can determine and test the proper settings.

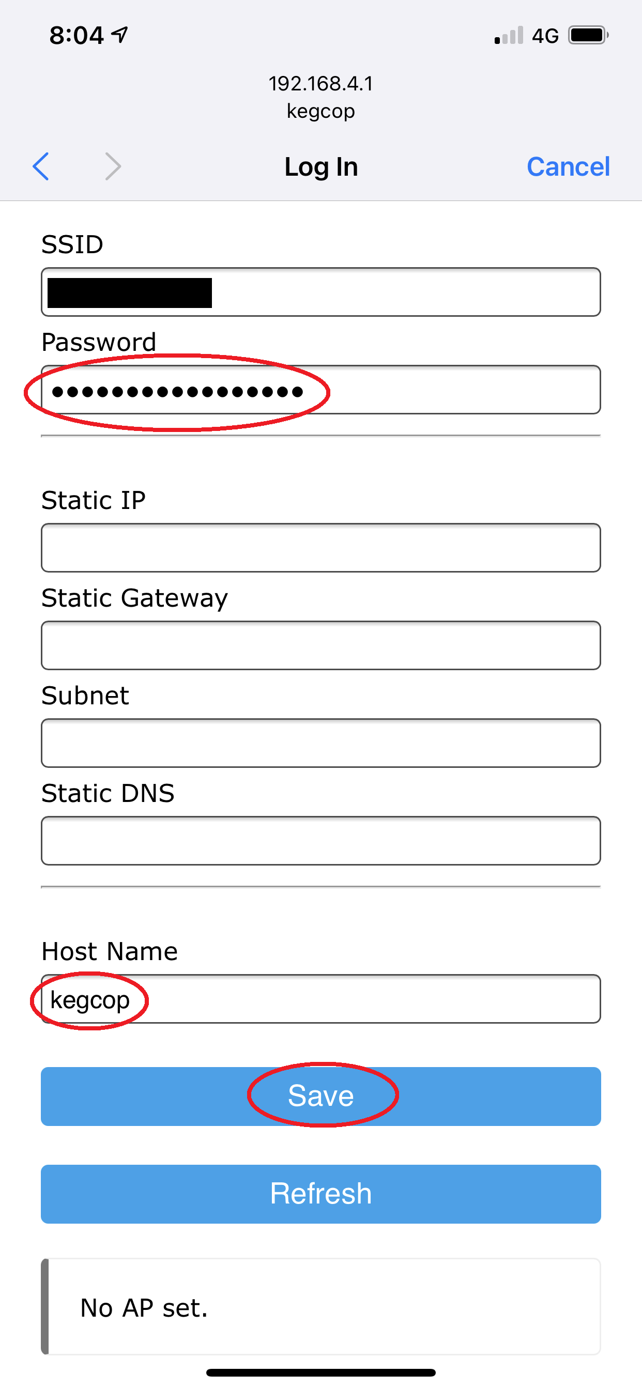
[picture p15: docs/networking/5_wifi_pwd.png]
```{image} 5_wifi_pwd.png
:align: center
:alt: WiFi Password
:scale: 20%
```

Click the "Save" button.

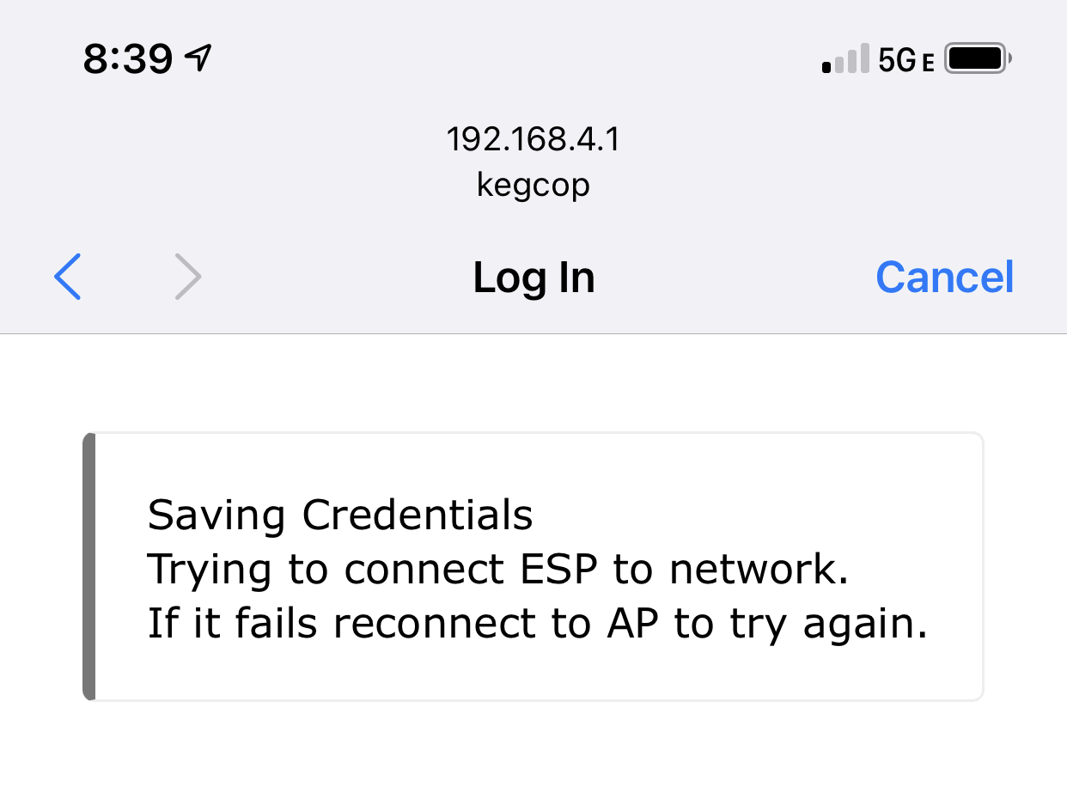
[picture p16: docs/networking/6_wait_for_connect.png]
```{image} 6_wait_for_connect.png
:align: center
:alt: Wait For Connect
:scale: 20%
```

The controller will attempt to connect to the network. If the connection is successful, the Keg Cop AP will go away, and your device should connect to your last known good connection. You may have to reconnect your computer or phone manually. In the case of the iPhone, if the Keg Cop does not connect to your local wireless, the AP will not terminate, and your browser will remain on this screen.  You can hit the back ("\<") arrow to return to the WiFi configuration and try again.

If all goes as expected, the controller's LED will flash as it performs various configuration steps, and finally, the LED will remain off. Here you may proceed. If you have issues, check the {ref}`troubleshooting <troubleshooting>` page for more information.

## Network Settings Change

At some point, you may need to change your WiFi settings. Remembering to do it while you are still able to connect to the application is simplest. However, you may raise the access point without being able to access the Keg Cop Application.

### Reset Settings

The easiest way to change settings is to access the Keg Cop web page.  In Settings > Advanced > Reset Wifi you may {ref}`reset wifi settings <resetwifi>`.  After that, you can re-join the Keg Cop soft AP and configure a new network.

### Re-Raise AP

If the Keg Cop controller cannot access the configured WiFi network, it should drop into AP mode and allow configuration. It will indicate this by the AP-mode flashing (0.5Hz) of the onboard LED.

If this does not work, or if you prefer, you may raise the AP by a double-reset press or an electrical connection.

#### Double-Reset Detect

If you press the reset button twice within three seconds, the device will enter AP mode and begin flashing (0.5Hz) the onboard LED.  The reset presses need not be fast; it will likely work more reliably if you leave 0.5-1.0 seconds between presses.

#### Electrical Connection

Take a piece of wire and short pin 13 to ground. Then with the wire connected, reset the controller by pressing the reset button or cycling power. The controller will detect pin 13 being low on startup, enter AP mode, and begin flashing (0.5Hz) the onboard LED.  You can disconnect the wire and proceed with the configuration.

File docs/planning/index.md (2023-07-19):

(planning)=

# Project Planning

Keg Cop is capable of a wide variety of configurations. Each has similar building blocks, and you may apply that methodology to a variety of applications. Here is a system with two flow meters, a room temp sensor, a keg temp sensor, a chamber sensor, cooling control, and a solenoid.

```{image} system.png
:align: center
:alt: System Diagram
:scale: 15%
```

It would be best if you did a little planning before you begin.  Keg Cop is configurable and extensible, and as such, you should know what you hope to achieve.

- **Tap Number Choice**: This is the most basic and most important decision. The controller choice for this project allowed up to nine pins for flow meters. The system works by utilizing up to three strings of three flowmeters each.  This optimization is a result of choosing easily-sourced Ethernet cables as the connectivity between boards.
- **Temp Sensor Choice**: Since this system provides temperature control of your keg chamber, temperature sensors are naturally supported and required for temperature control. Keg Cop supports up to five temperature sensors, including one for room temperature.
- **Main Board - One main board per system:**: It provides a single Ethernet going to the flowmeter chain and another Ethernet port connecting to the chamber sensors. A temperature sensor for Room temperature mounted to the board.
- **Sensor/Meter Boards - Connectors to the physical aspects of the system:**
  : - Daisy-Chain Boards: These small boards, one per flowmeter, connect the flowmeter(s) into the system. There is an "In" and an "Out" connector, creating a chain of up to nine sensors. The first on the chain is always number one, and so on.
    - Sensor Board: This is a breakout board for connecting up to five temperature sensors.

The BOM for the electronics may be found on the {doc}`PCB Assembly </pcbassembly/index>` page.

## Flowmeters

The flowmeter is probably the single most important and yet the most challenging part to source. It's not because flowmeters are hard to find; it's because there are so many choices. Your choices will dictate some of the operations choices for the application.

Keg Cop will support a different flowmeter on each tap if that's how you want to go.

You can choose from any number of flowmeters using a single data (pulse/frequency) line and powered from 3V3. Some choices used by the homebrewing community include:

- Swissflow [SF800] Low-Pressure Flow Meter
- [YF-S401] Water Flow Sensor Meter Flowmeter Coffee Dispenser Counter 0.3-6 L/min (eBay)
- Liquid Flow Meter - Plastic 1/2" NPS Threaded ID: [828] (Adafruit)

While one or two of the above links may eventually grow stale, what is listed should give you enough information to find a suitable device. Swissflow is probably the most expensive device. However, it is likely the most accurate one available. To be completely transparent, they helped my development by defraying a portion of my meters' expenses. I would have purchased them at the list price if they had not.

Buy once, cry once, as my grandfather used to say.

## A Practical Example

Take, for example, my three-tap kegerator. I need to decide whether or not I will use temperature sensors. I do want to use Keg Cop to control my Kegerator temperatures, so I know I need both a sensor board and one daisy chain board per flow meter.  My setup therefore is:

- One main board
- One Sensors board
- Three Daisy Chain boards with flowmeters

If you have a similar setup, you may always add new Daisy Chain boards as needed. The most appropriate installation uses one Keg Cop per kegerator/keezer.  If you are fortunate enough to have more than one kegerator, plan for separate Keg Cop systems.

## Why This Approach?

I polled the community some time back, asking [how many kegs people had in their kegerator/keezer](https://www.homebrewtalk.com/threads/how-many-kegs-in-your-keezer-kegerator.672039/). I learned that most people have four kegs per unit (27.8%) with three kegs coming in a close second (25%).  Eighty-seven percent (87.5) of the respondents had seven or fewer kegs.  In hindsight, I should have set up the poll with a clear separation between having eight kegs and having nine or more, but nobody is perfect.

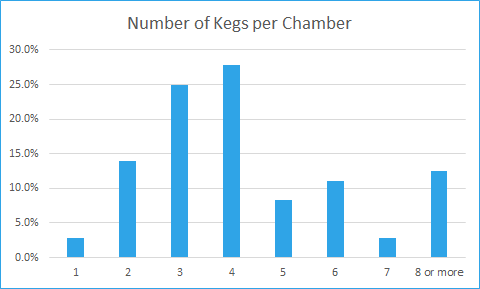
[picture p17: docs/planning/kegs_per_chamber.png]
```{image} kegs_per_chamber.png
:align: center
:alt: Kegs per Chamber
:scale: 100%
```

In another thread, I asked [how many kegerators or keezers people had](https://www.homebrewtalk.com/threads/how-many-kegerators-keezers.672043/).  This poll showed that the vast majority of homebrewers have a single chamber (52.2%), with less than a quarter of the respondents (21.7%) having two. I feel that the approach I have taken of one per chamber is reasonable and will not be burdensome.

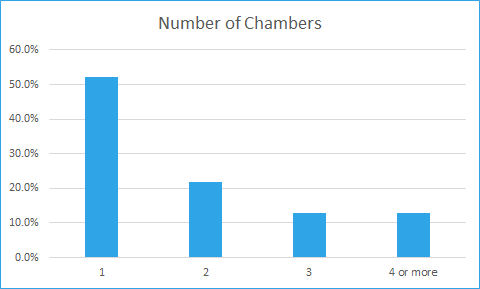
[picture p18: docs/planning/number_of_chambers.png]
```{image} number_of_chambers.png
:align: center
:alt: Kegs per Chamber
:scale: 100%
```

There are always edge cases, people with morgue-sized chest freezers in each room with ten kegs. My feeling is that these people have already invested a significant amount in their systems. These homebrewers are used to things just being more complicated at scale, and having multiple Keg Cops is the least of their worries.

## Design Limitations

There are also some practical considerations to these design constraints:

- **Off the shelf cabling:** The cabling method is what I consider a shortcoming in some DIY projects. One often finds instructions to "connect the widget arm to the maniform" without any indication of how to do it. Illustrations invariably show a rainbow of DuPont wires plugged into a breadboard. That's fine for development work but does not address real-life needs. People need a prescriptive method to connect components. It should be simple, prevent crossed circuits, and not have an entry cost for tooling, which creates hidden costs. Ethernet cables check almost all our needs. They are straight-through (where phone cords have a crossover) and can be purchased locally or online.  They are also available in many lengths and have a reasonably secure connection mechanism.
- **Cabling Capacity:** Having chosen the prescribed cabling, this does create an inherent limitation. An Ethernet cable has eight wires. A flowmeter has power and ground, shared across each meter, plus a discrete data line. Each data line needs a paired ground with which it is twisted within the bundle to prevent electrical interference.  That means a single Ethernet cable can serve a maximum of three flowmeters. A similar situation exists with the temperature sensors. Using all available temperature sensor slots consumes seven of the eight available wires.
- **Controller Capacity:**
  : - A controller has a given number of pins with which to interact with the physical world. Some pins also have a function internal to the controller or the development board (such as the LED.) This project uses almost all available pins on the chosen ESP32 development board.
    - The OneWire sensors I use for temperatures could work with all sensors on a single wire for data (hence the "OneWire" name.)  You are familiar with the slight inconvenience this poses if you have used one of the various fermentation temperature controllers. You have to connect one sensor at a time and assign its use, or heat/cool one sensor at a time so that you can label it. Each sensor has an internal address that allows it to be assigned to a specific use or name; however, figuring out which one is a little cumbersome. I wanted a more straightforward method of one sensor per pin so that there is an explicit physical configuration without such addressing concerns. Because of this approach, I have reserved five controller pins for temperature sensors.
    - The flow meters do not have any method of resolving a sensor. The data pin pulses as the flow is detected. On the controller, we use one pin per sensor to catch each pulse independent of the others. Therefore, I have reserved nine pins for flow meters.
    - Temperature control means that there needs to be a method of turning on and off the cooling. One pin is used for this to control a relay.
    - Solenoid control is a feature that exists in many of the previous keg display systems. Because of the keg lines' proximity, this device seemed like the appropriate place to put the solenoid control. We use one pin for this, intended to turn on or off all solenoids at once using a relay.

Some of the pins available to us are not appropriate for all uses. Some pins will prevent the controller from booting if held high or low as it would be if connected to a sensor or flow meter. Some pins will be set high or low during the boot process regardless of what the program will do when it starts. Such a pin attached to the cooling relay may cause the refrigerator compressor to short-cycle.

I do not doubt that some crafty person might look at this and devise a more glamorous approach. For instance, there are I2C boards that would extend the system's capabilities. My final criteria for this design is to have a simple, compact design, capable of providing a prescriptive path to success for the average DIYer. Taking a very simplistic, 1:1 approach to interfacing software to the physical world meets this goal. If you are one of those people who think you can do it better, you have my blessing to fork the project and do your best.

[828]: https://www.adafruit.com/product/828
[sf800]: http://www.swissflow.com/sf800.html
[yf-s401]: https://www.ebay.com/itm/YF-S401-Water-Flow-Sensor-Meter-Flowmeter-Coffee-Dispenser-Counter-0-3-6-L-min/282112630770

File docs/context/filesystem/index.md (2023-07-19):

(filesystem_information)=
# Filesystem Information

By manually navigating to `/fs/` or by utilizing the link on the *About* page, you will gain access to a powerful filesystem editor.

You must authenticate to this page; the default (and currently static) credentials are:

- Username: `admin`
- Password: `p@ssword`

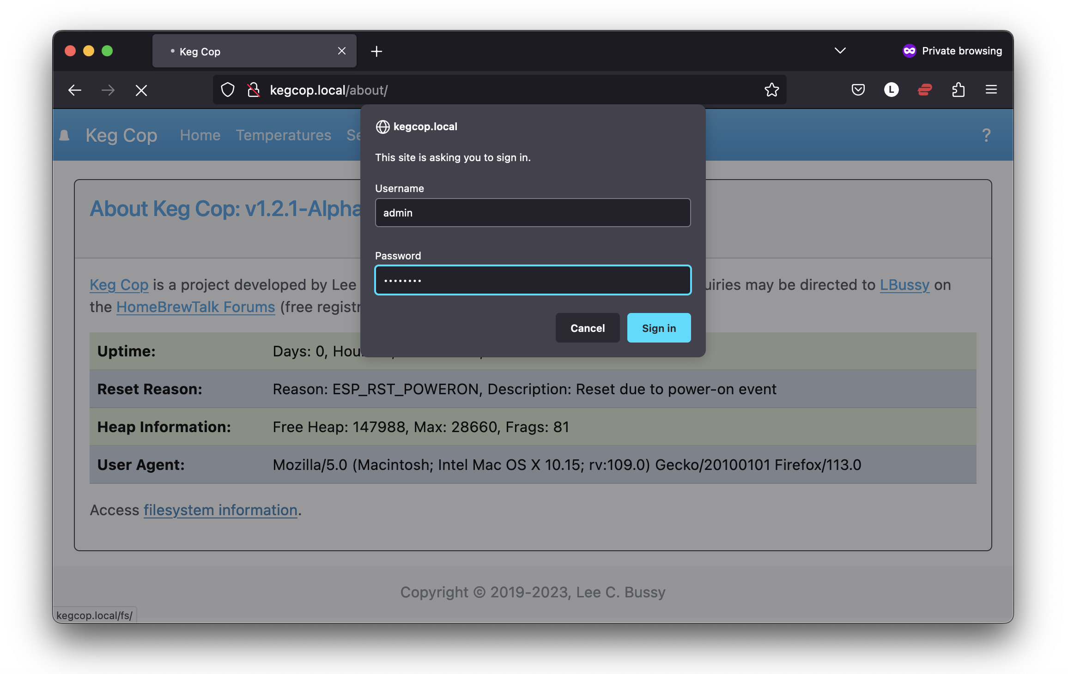
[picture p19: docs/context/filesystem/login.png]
```{image} login.png
:align: center
:alt: About Keg Cop
:scale: 25%
```

As with all such functions available on this system, the security inherent in the system is unsuitable to allow Internet exposure.  Use appropriate precautions.

## Filesystem Information

After authentication, the page will present you with basic filesystem information.

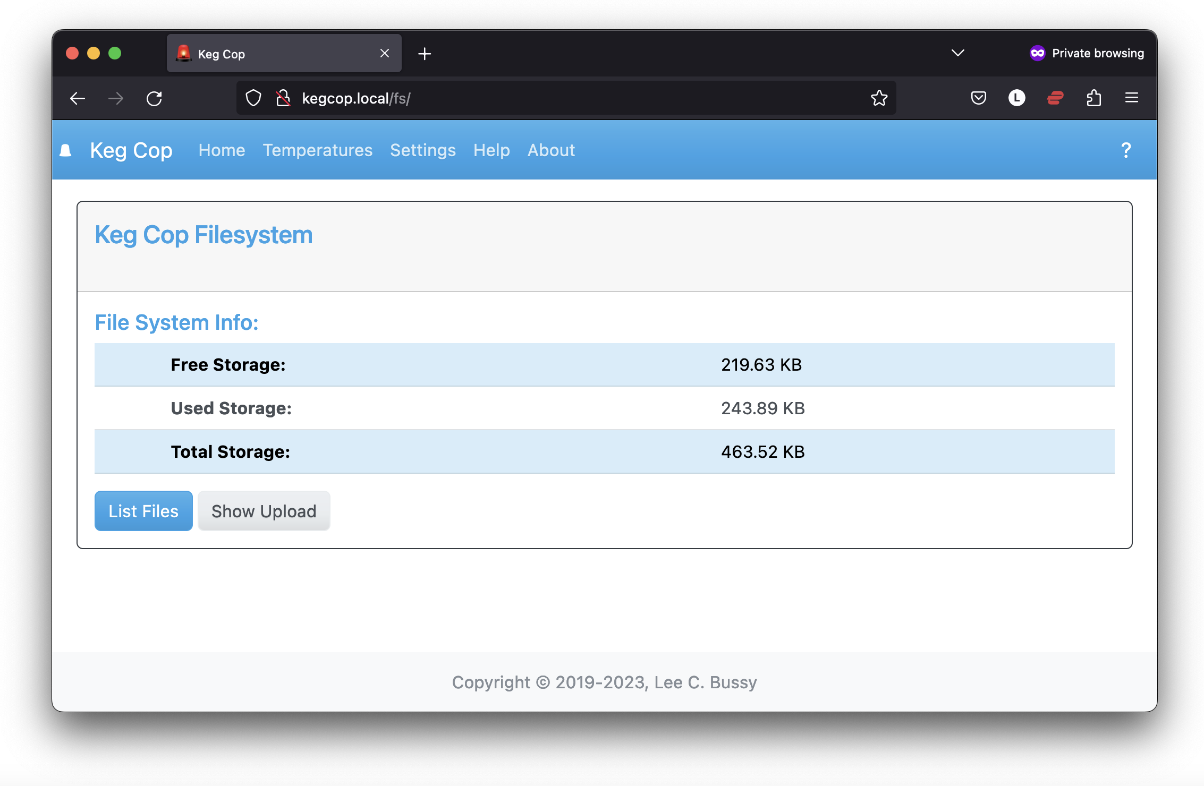
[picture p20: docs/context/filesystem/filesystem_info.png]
```{image} filesystem_info.png
:align: center
:alt: File System Info
:scale: 25%
```

This page shows the following information about the filesystem partition:

- Free Storage
- Used Storage
- Total Storage

Two additional buttons are available:

- List Files
- Show Upload

# List Files

This button will toggle a page showing every file on the filesystem.  For each file, the file size, as well as two buttons, are available:

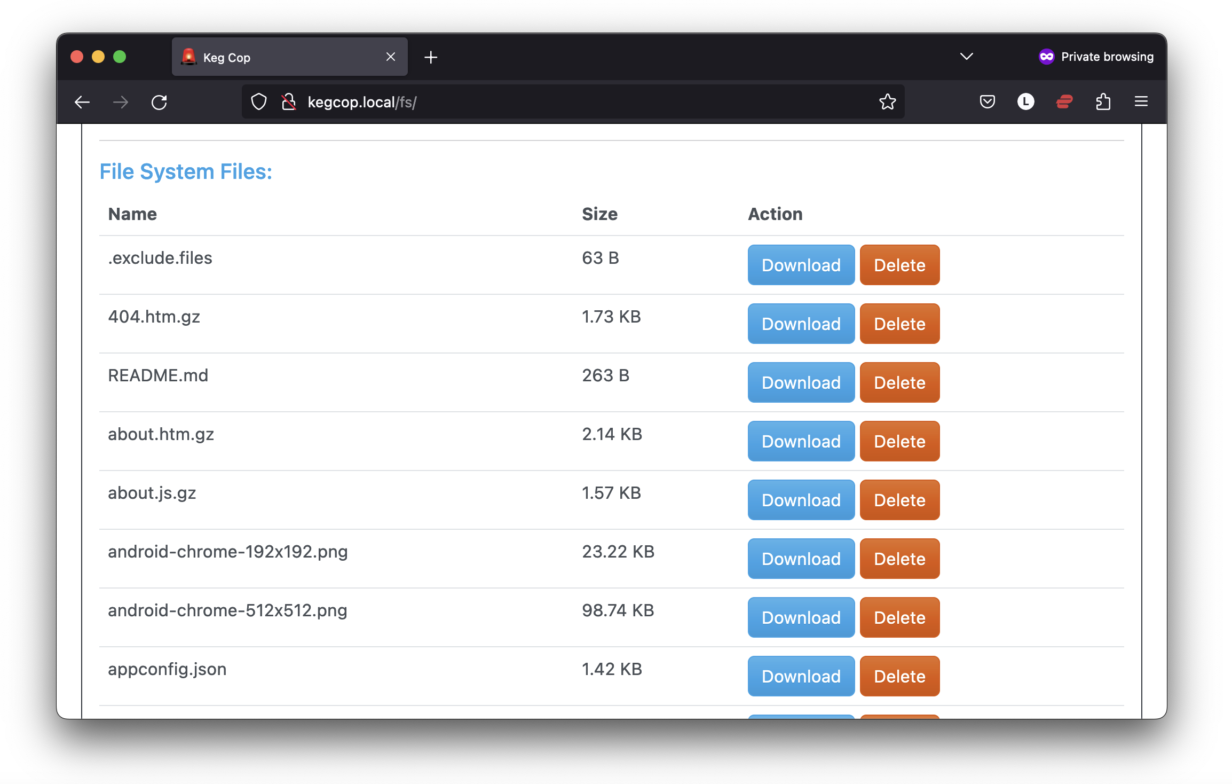
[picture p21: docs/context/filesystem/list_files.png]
```{image} list_files.png
:align: center
:alt: File System Info
:scale: 25%
```

- **Download** - Allows downloading the file to your local computer.  Your browser may prompt you to allow pop-ups to complete the download.
- **Delete** - This will delete the file from the filesystem with a prompt ensuring you intend to delete the file.  Deleting files may significantly impact the system and render the user interface unusable.  ***Use this at your own risk.***  If you affect your functionality, you may have to re-flash your controller.

# Show Upload

This button allows uploading a *single* file to the filesystem.  If the file already exists, the upload will overwrite it without any additional prompt.

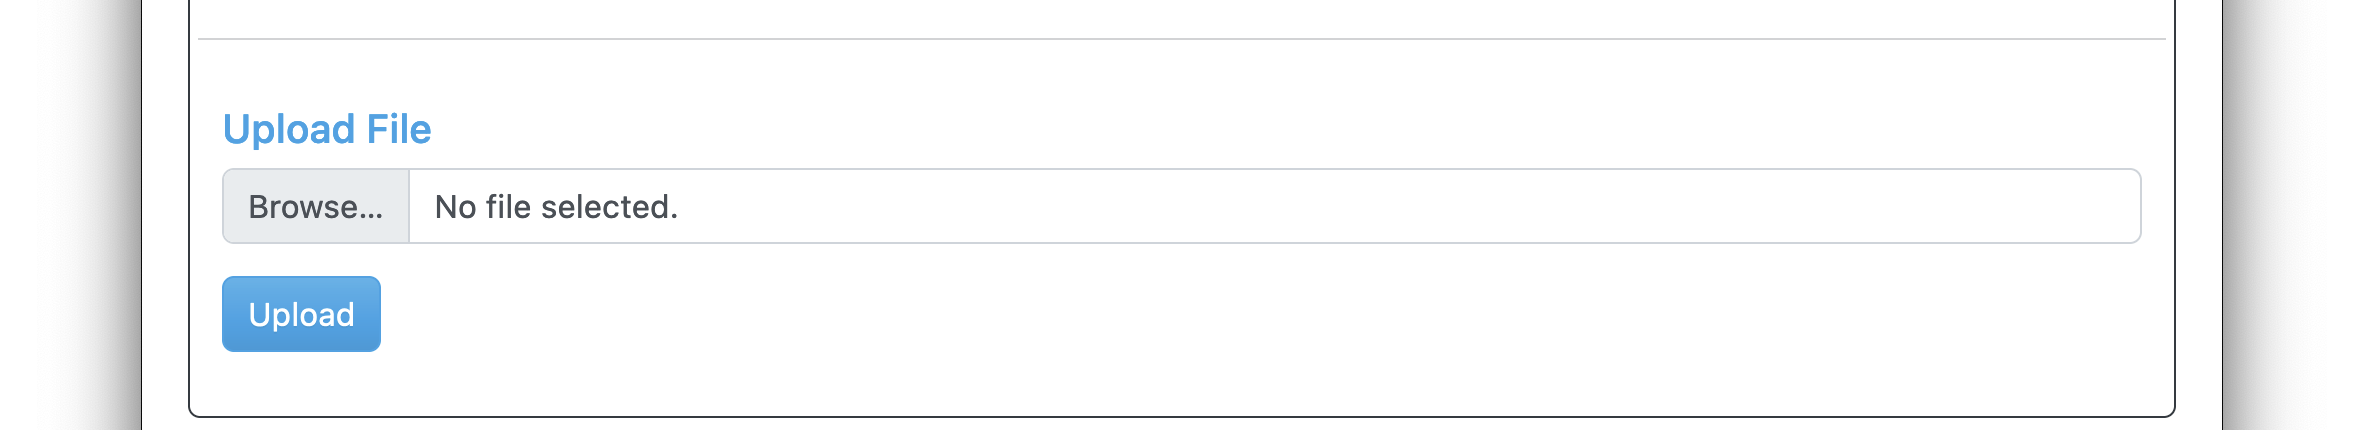
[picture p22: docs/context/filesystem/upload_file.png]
```{image} upload_file.png
:align: center
:alt: File System Info
:scale: 25%
```

## Ninja Switch

Within IT, some folks use the term "ninja switch" to refer to advanced functions that may not be wholly documented or supported.  Uploading Files here is one such ninja switch.

While it is unlikely that the author can consider all such potential uses, this functionality currently be used to backup and restore system configuration.  If you use it this way, you must immediately hard reset the controller (either with the physical reset button or a power cycle).  Otherwise, the regular operation of the system may overwrite the configuration you upload.

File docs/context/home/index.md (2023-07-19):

(home)=

```{eval-rst}
.. include:: <xhtml1-symbol.txt>
```

# Home Page

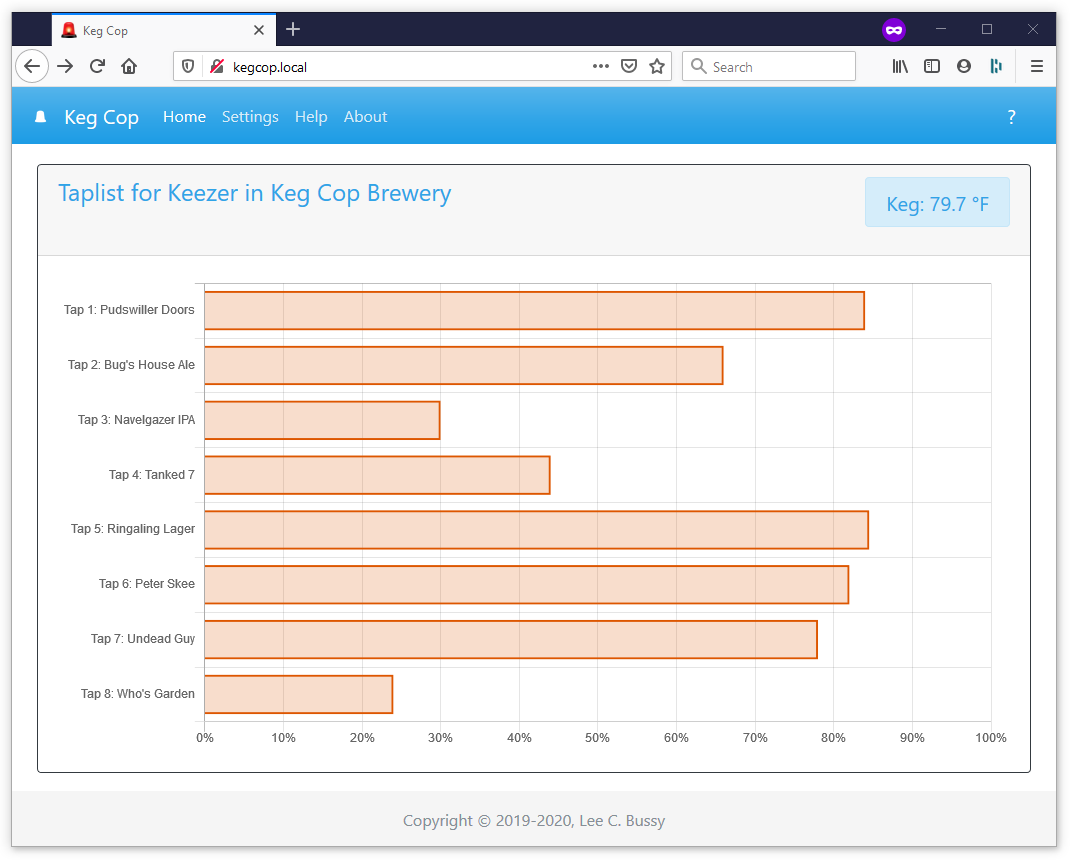
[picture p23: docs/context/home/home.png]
```{image} home.png
:align: center
:alt: Home Page
:scale: 50%
```

The Keg Cop home page is displayed when you first connect via your chosen web browser.  You will see a main menu across the top border if you connect with a standard desktop web browser.  If in a mobile or portrait mode browser window, the list displays when you click the hamburger bar ({{ equiv }}) in the top-right corner.

In the top-left side of the main container is a title concatenated from the {ref}`kegerator <controller>` and {ref}`brewery name <controller>` (e.g. "Main Kegerator in Silver Fox Brewery.")

On the right side of this container is the current control point temperature if used.  The block around the temperature indicates the temperature control status. You may also hover over this section for a tooltip explaining the state.

Within the page, you will see a list of the active taps on your system.  The bars will show the relative amount of beverage remaining for each tap.  The bars themselves have a mouseover effect that will display a tooltip containing detailed information.

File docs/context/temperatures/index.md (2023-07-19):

(temperatures)=

# Temperatures

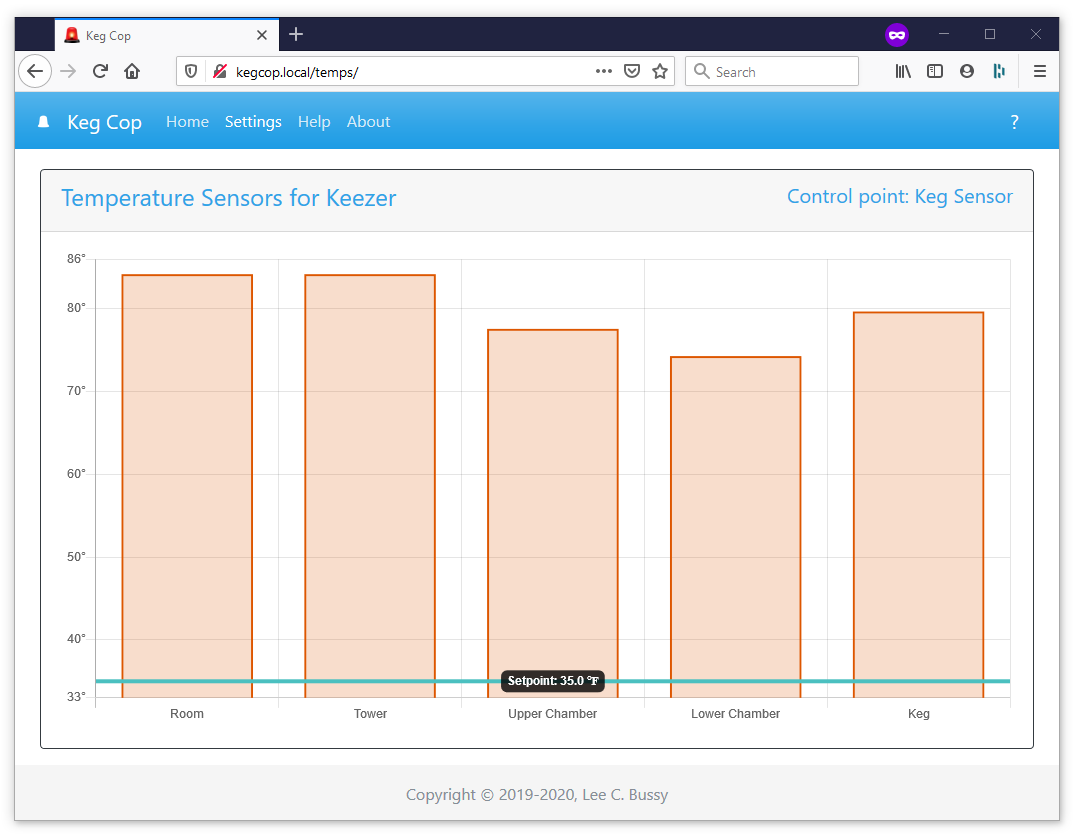
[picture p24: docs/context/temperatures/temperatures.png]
```{image} temperatures.png
:align: center
:alt: System Temperatures
:scale: 50%
```

If you have configured the Keg Cop system with temperature sensors, you may navigate to this page with the Temperature Sensor link on the main menu.  Its presence in the main menu bar is dynamic, so it will only appear after a page loads completely.

There is also a link to the Temperature page via the temperature display and cooling status box in the top-right corner of the home page.

The Temperature Sensors page displays a bar for each active temperature sensor.  If you have configured the system to control temperatures, a horizontal bar will appear across the chart showing the setpoint.

The selected control point will appear in the top-right of the box and link to the Temperature Control settings page.

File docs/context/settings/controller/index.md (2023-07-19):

(controller)=

# Controller Settings

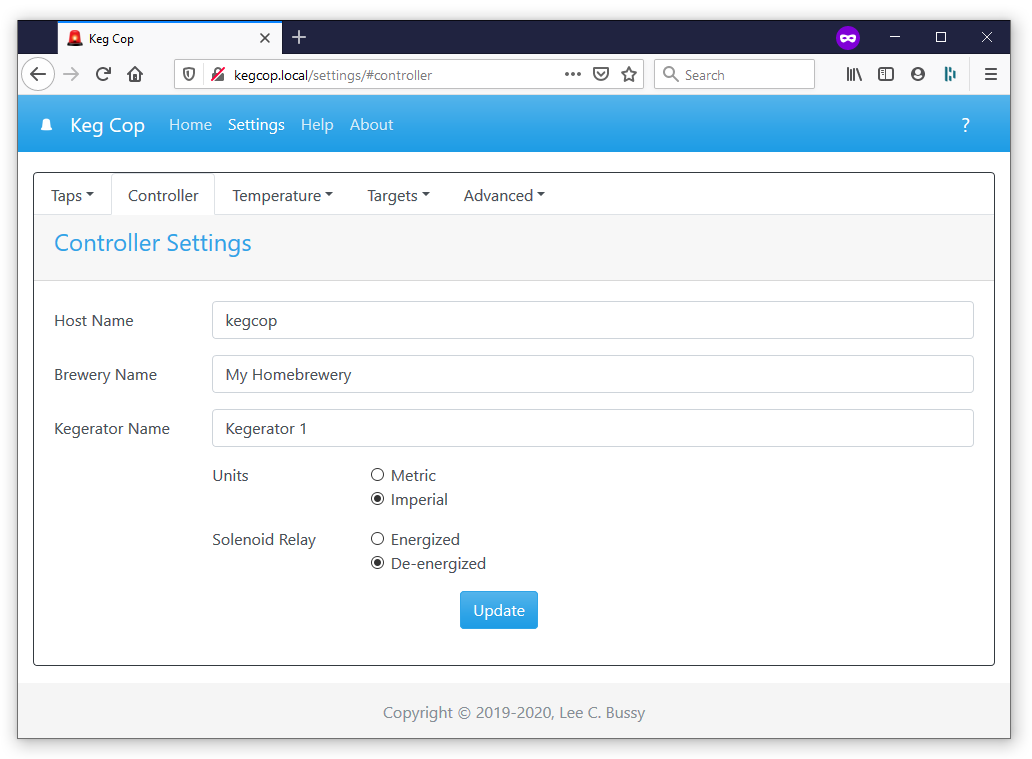
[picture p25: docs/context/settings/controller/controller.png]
```{image} controller.png
:align: center
:alt: Controller Settings
:scale: 50%
```

The Controller Settings page allows configuration of settings which control the top-level settings of the system:

- **Host Name**: This is the network hostname, to which you will connect as  *\{hostname}*.local. Do not include the .local portion; the mDNS system will append this automatically.  This name must be unique on the network, or unexpected behavior may result.  Most computer systems and mobile devices support mDNS. For more information, please see the {ref}`mDNS FAQ <faq-mdns>`.
- **Brewery Name**: This is displayed on the {ref}`main page <home>`. It concatenates with the Kegerator name, e.g., "*Taplist for Kegerator in Silver Fox Brewery.*"
- **Kegerator Name**: This displays on the main page. It concatenates with the Brewery name, e.g., e.g., "*Taplist for Kegerator in Silver Fox Brewery.*" This name reports to any upstream system.
- **Units**:
  : - **Metric**: Volume reports in liters and milliliters, the temperature in degrees Celcius, and you will enter the flowmeter calibration in pulses per liter.
    - **Imperial**: Volume reports in gallons and ounces, the temperature in degrees Fahrenheit, you will enter the flowmeter calibration in pulses per gallon.
- **Solenoid Relay**: This will energize or de-energize a relay. This setting controls a solenoid or bank of solenoids to turn the beverage flow on or off. I have provided this point for convenience; I intend for an upstream system to control it.

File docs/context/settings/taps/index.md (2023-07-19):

(taps)=

# Tap Settings

The first choice on the Settings screen is a drop-down tab labeled Taps.  Clicking on this will allow you to configure taps number one through nine individually.

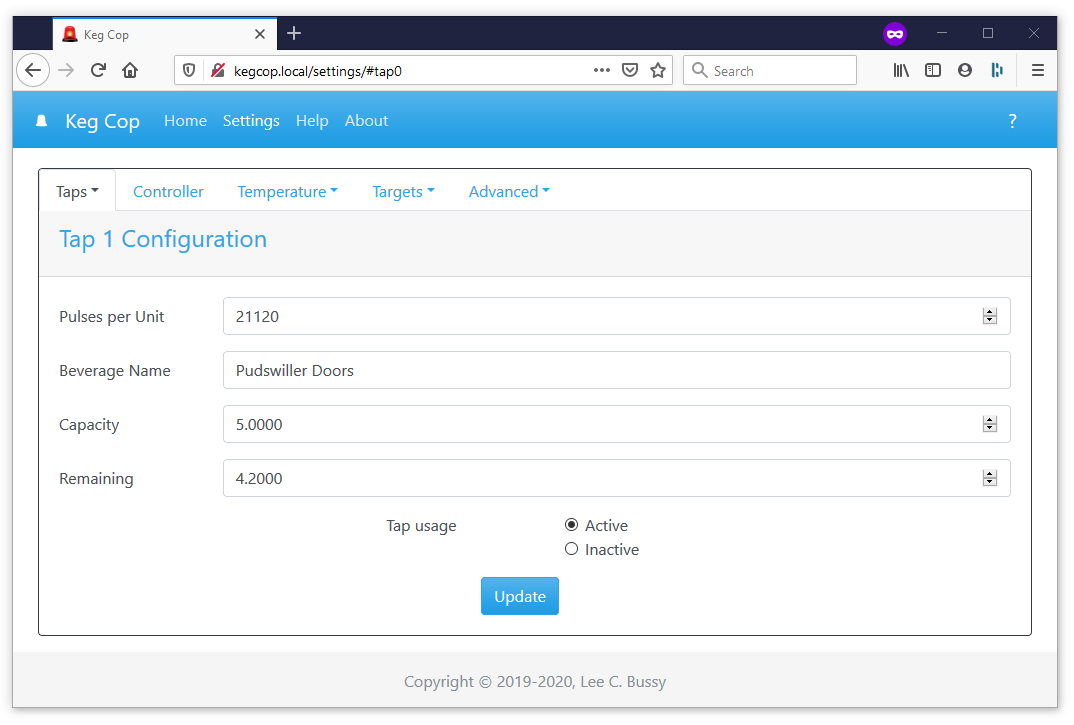
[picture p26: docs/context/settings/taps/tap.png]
```{image} tap.png
:align: center
:alt: Tap UI
:scale: 50%
```

Enter the pulses per gallon/liter, the name of the beverage on tap, and the keg's capacity. You may enter the initial amount remaining in the keg when you tap it or adjust it as needed. The amount remaining will debit automatically during use.

Setting the keg as active/inactive will determine if the keg reports to the upstream system and if it displays on the home page.  The keg will be set to inactive automatically when a kick event is detected.

## PPG/PPL Calibration

See the {ref}`flowmeter calibration <calibrate>` page for more information on calculating the PPG/PPL.

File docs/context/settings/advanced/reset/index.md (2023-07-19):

(reset)=

# Reset Controller

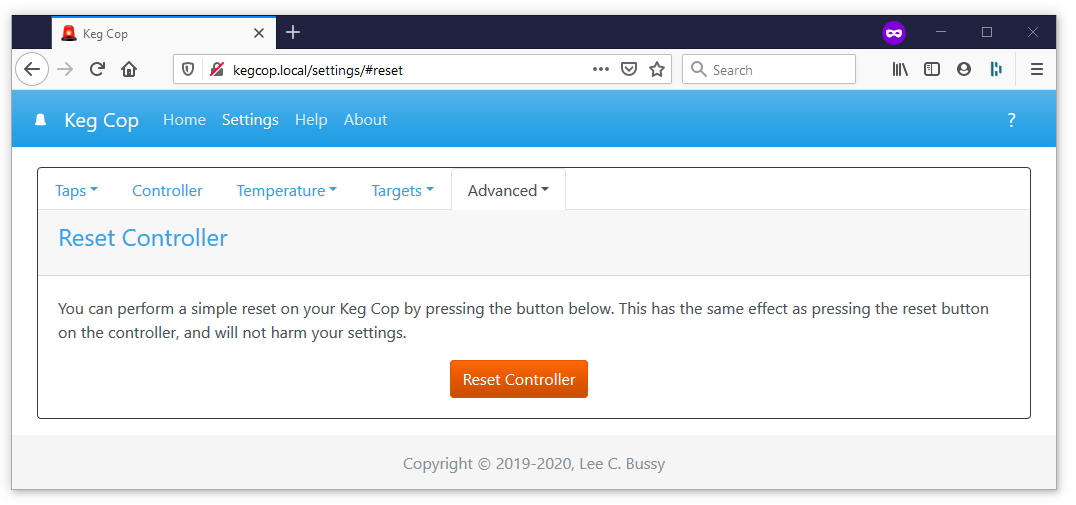
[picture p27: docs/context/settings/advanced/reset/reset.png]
```{image} reset.png
:align: center
:alt: Reset Controller
:scale: 50%
```

Clicking the "Reset Controller" button in this UI will perform the same function as pressing the reset button on the controller. The controller will retain all settings.

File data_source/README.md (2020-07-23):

Keg Cop Logo Keg Cop (http://www.kegcop.com/)

# Web Pages

These are the pages that are loaded onto the controller to provide user interaction functionality with the Keg Cop application.

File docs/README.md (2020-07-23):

Keg Cop Logo Keg Cop (http://www.kegcop.com/)

# Keg Cop Documentation



The documentation here is a source file repository that is compiled into a readable format. Unless you intend to work with the source files, please view the documentation at the [Keg Cop documentation](https://docs.kegcop.com) pages.

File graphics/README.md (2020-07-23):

Keg Cop Logo Keg Cop (http://www.kegcop.com/)

# Graphics

These are the working files, mostly for the web pages, used in this project.  Generally speaking, there's nothing of interest for most folks in this folder.

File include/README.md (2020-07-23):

Keg Cop Logo Keg Cop (http://www.kegcop.com/)

# Includes

This directory is intended for project header files.

A header file is a file containing C declarations and macro definitions
to be shared between several project source files. You request the use of a
header file in your project source file (C, C++, etc) located in `src` folder
by including it, with the C preprocessing directive `#include'.

```src/main.c

#include "header.h"

int main (void)
{
 ...
}
```

Including a header file produces the same results as copying the header file
into each source file that needs it. Such copying would be time-consuming
and error-prone. With a header file, the related declarations appear
in only one place. If they need to be changed, they can be changed in one
place, and programs that include the header file will automatically use the
new version when next recompiled. The header file eliminates the labor of
finding and changing all the copies as well as the risk that a failure to
find one copy will result in inconsistencies within a program.

In C, the usual convention is to give header files names that end with `.h'.
It is most portable to use only letters, digits, dashes, and underscores in
header file names, and at most one dot.

Read more about using header files in official GCC documentation:

* Include Syntax
* Include Operation
* Once-Only Headers
* Computed Includes

https://gcc.gnu.org/onlinedocs/cpp/Header-Files.html

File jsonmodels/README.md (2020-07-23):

Keg Cop Logo Keg Cop (http://www.kegcop.com/)

# JSON Models

This folder containes references and examples of the JSON configurations used within this project. Ubless you are a glutton for punishment, most people will find [the documentation](https://docs.kegcop.com) a better source of information for the API.

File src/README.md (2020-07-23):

Keg Cop Logo Keg Cop (http://www.kegcop.com/)

# Source Files

These are the C++ source files for Keg Cop.

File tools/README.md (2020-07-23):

Keg Cop Logo Keg Cop (http://www.kegcop.com/)

# Tools

Files within this directory are generally used for maintenance of the project or website.

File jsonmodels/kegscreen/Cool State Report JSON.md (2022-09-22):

Cool State Report JSON Model:
==============================

JSON Definition:
----------------

```
{
    "api":"xxxxxxxxxxxxxxxxxxxxxxxxxxxxxxxx",
    "guid":"xxxxxxxx",
    "hostname":"xxxxxxxxxxxxxxxxxxxxxxxxxxxxxxxx",
    "breweryname":"xxxxxxxxxxxxxxxxxxxxxxxxxxxxxxxxxxxxxxxxxxxxxxxxxxxxxxxxxxxxxxxx",
    "kegeratorname":"xxxxxxxxxxxxxxxxxxxxxxxxxxxxxxxxxxxxxxxxxxxxxxxxxxxxxxxxxxxxxxxx",
    "reporttype":"xxxxxxxxxxxxxxxx",
    "coolstate":99,
    "tfanstatus":99
}
```

Size:
-----

```
Serialize:  384
Deserialize:  512
```

Deserializing / Parsing / Loading:
----------------------------------

```
// Stream& input;

StaticJsonDocument<512> doc;

DeserializationError error = deserializeJson(doc, input);

if (error) {
  Serial.print("deserializeJson() failed: ");
  Serial.println(error.c_str());
  return;
}

const char* api = doc["api"]; // "xxxxxxxxxxxxxxxxxxxxxxxxxxxxxxxx"
const char* guid = doc["guid"]; // "xxxxxxxx"
const char* hostname = doc["hostname"]; // "xxxxxxxxxxxxxxxxxxxxxxxxxxxxxxxx"
const char* breweryname = doc["breweryname"];
const char* kegeratorname = doc["kegeratorname"];
const char* reporttype = doc["reporttype"]; // "xxxxxxxxxxxxxxxx"
int coolstate = doc["coolstate"]; // 99
bool fanon = doc["fanon"]; // false
```

Serializing / Saving:
---------------------

```
StaticJsonDocument<384> doc;

doc["api"] = "xxxxxxxxxxxxxxxxxxxxxxxxxxxxxxxx";
doc["guid"] = "xxxxxxxx";
doc["hostname"] = "xxxxxxxxxxxxxxxxxxxxxxxxxxxxxxxx";
doc["breweryname"] = "xxxxxxxxxxxxxxxxxxxxxxxxxxxxxxxxxxxxxxxxxxxxxxxxxxxxxxxxxxxxxxxx";
doc["kegeratorname"] = "xxxxxxxxxxxxxxxxxxxxxxxxxxxxxxxxxxxxxxxxxxxxxxxxxxxxxxxxxxxxxxxx";
doc["reporttype"] = "xxxxxxxxxxxxxxxx";
doc["coolstate"] = 99;
doc["fanon"] = false;

serializeJson(doc, output);
```

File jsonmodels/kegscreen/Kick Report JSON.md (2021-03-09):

Kick Report JSON Model:
===========================

JSON Definition:
----------------

```
{
    "api":"xxxxxxxxxxxxxxxxxxxxxxxxxxxxxxxx",
    "guid":"xxxxxxxx",
    "hostname":"xxxxxxxxxxxxxxxxxxxxxxxxxxxxxxxx",
    "breweryname":"xxxxxxxxxxxxxxxxxxxxxxxxxxxxxxxxxxxxxxxxxxxxxxxxxxxxxxxxxxxxxxxx",
    "kegeratorname":"xxxxxxxxxxxxxxxxxxxxxxxxxxxxxxxxxxxxxxxxxxxxxxxxxxxxxxxxxxxxxxxx",
    "reporttype":"xxxxxxxxxxxxxxxx",
    "tapid":99
}
```

Size:
-----

```
128 or 384
```

Deserializing / Parsing / Loading:
----------------------------------

```
// char* input;
// size_t inputLength; (optional)

StaticJsonDocument<128> doc;

DeserializationError error = deserializeJson(doc, input, inputLength);

if (error) {
  Serial.print(F("deserializeJson() failed: "));
  Serial.println(error.f_str());
  return;
}
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

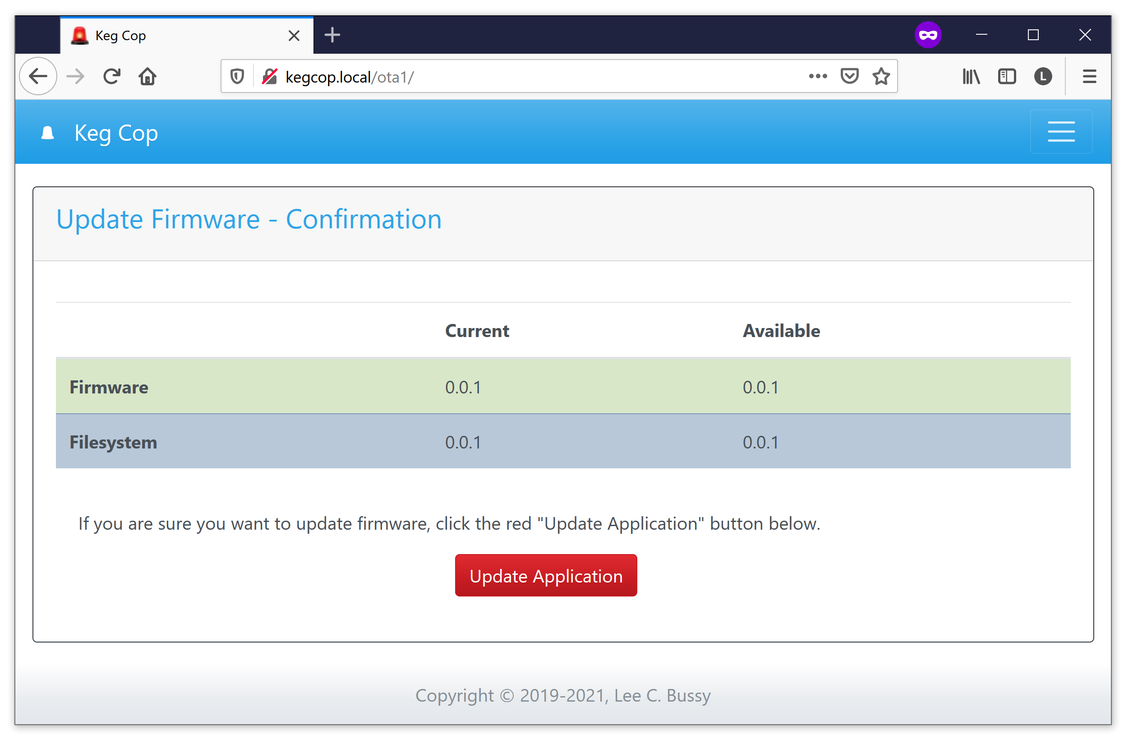
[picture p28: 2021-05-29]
docs/context/settings/advanced/update/update.png

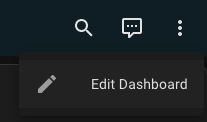
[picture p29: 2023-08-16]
docs/homeassistant/edit_dash.png

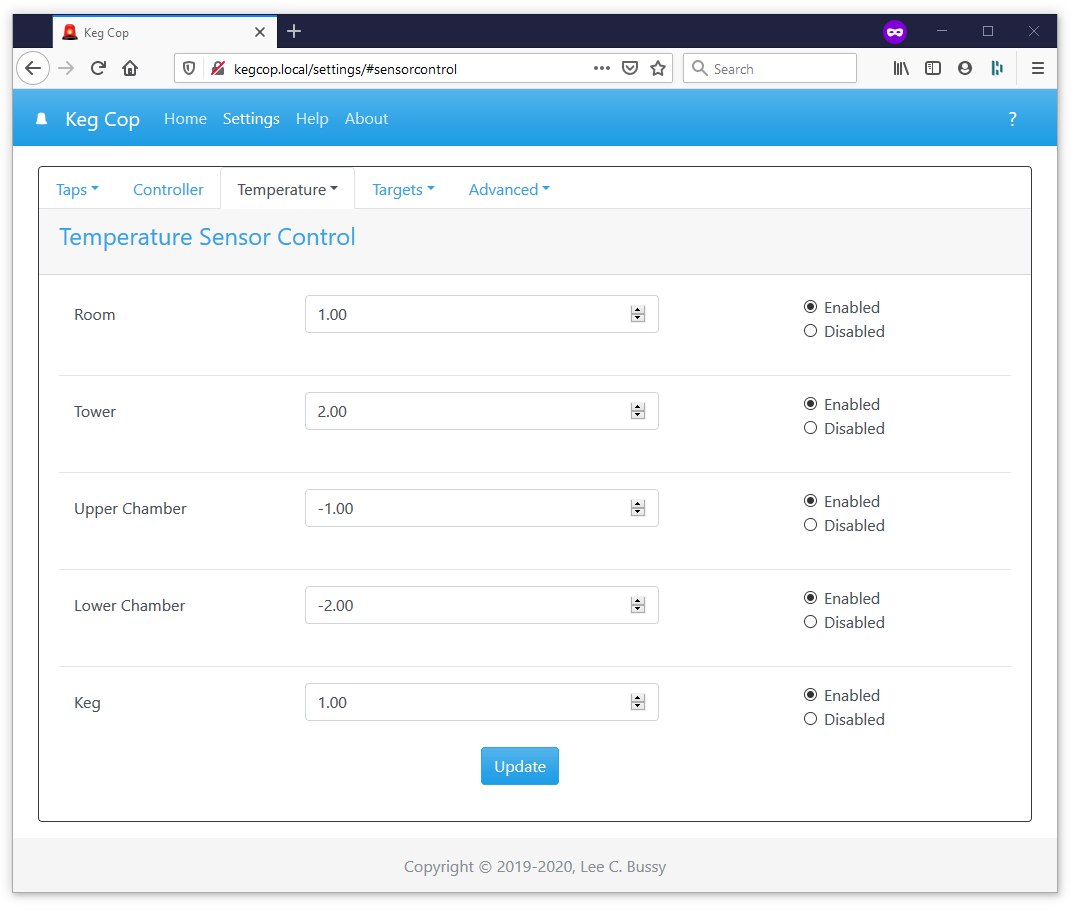
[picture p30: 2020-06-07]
docs/context/settings/temperature/sensors/sensors.png

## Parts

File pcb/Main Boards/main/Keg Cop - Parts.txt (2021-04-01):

Partlist exported from C:/Users/lee/OneDrive/Documents/GitHub/keg-cop/pcb/Main Boards/main/Keg Cop - Main.sch at 3/30/2021 6:56 PM

Part  Value     Device               Package        Description                                                                                 ARROW_PART_NUMBER ARROW_PRICE-STOCK DESCRIPTION                           HEIGHT MANUFACTURER_NAME MANUFACTURER_PART_NUMBER MF MOUSER_PART_NUMBER MOUSER_PRICE-STOCK                                                                                     MPN     OC_FARNELL OC_NEWARK POPULARITY PROD_ID VALUE
C1    0.1μF     CAP_CERAMIC_2.54     CAP_PTH-2.54                                                                                                                                                                                                                                                                                                                                                                                                             
C2    1.0μF     CAP_CERAMIC_2.54     CAP_PTH-2.54                                                                                                                                                                                                                                                                                                                                                                                                             
C3    0.1μF     CAP_CERAMIC_2.54     CAP_PTH-2.54                                                                                                                                                                                                                                                                                                                                                                                                             
C4    1.0μF     CAP_CERAMIC_2.54     CAP_PTH-2.54                                                                                                                                                                                                                                                                                                                                                                                                             
D32   Lolin D32 WEMOS-D32D32_NO_BATT D32_NO_BATT    D32_REVERSE is a Reverse silkscreen for placing the Wemos D32 on the underside of the board                                                                                                                                                                                                                                                                                                               
IC1   DS18B20+  DS18B20+             TO-92          DS18B20 prog thermometer 1-Wire, TO92                                                       DS18B20+                            DS18B20 prog thermometer 1-Wire, TO92 mm     Maxim Integrated  DS18B20+                    700-DS18B20+       https://www.mouser.co.uk/ProductDetail/Maxim-Integrated/DS18B20%2b?qs=7H2Jq%252ByxpJKegCKabDbglA%3D%3D                                                      
POWER 2-PIN     HDR-2                HDR-2_VERT                                                                                                                                                                                                                                                                                                                                                                                                               
R1    2.2kΩ     RESISTORAXIAL-0.3    AXIAL-0.3      Generic Resistor Package                                                                                                                                                                                                                                                                                                                                                                                  
R2    2.2kΩ     RESISTORAXIAL-0.3    AXIAL-0.3      Generic Resistor Package                                                                                                                                                                                                                                                                                                                                                                                  
R3    2.2kΩ     RESISTORAXIAL-0.3    AXIAL-0.3      Generic Resistor Package                                                                                                                                                                                                                                                                                                                                                                                  
R4    2.2kΩ     RESISTORAXIAL-0.3    AXIAL-0.3      Generic Resistor Package                                                                                                                                                                                                                                                                                                                                                                                  
R5    2.2kΩ     RESISTORAXIAL-0.3    AXIAL-0.3      Generic Resistor Package                                                                                                                                                                                                                                                                                                                                                                                  
R6    2.2kΩ     RESISTORAXIAL-0.3    AXIAL-0.3      Generic Resistor Package                                                                                                                                                                                                                                                                                                                                                                                  
R7    2.2kΩ     RESISTORAXIAL-0.3    AXIAL-0.3      Generic Resistor Package                                                                                                                                                                                                                                                                                                                                                                                  
R8    2.2kΩ     RESISTORAXIAL-0.3    AXIAL-0.3      Generic Resistor Package                                                                                                                                                                                                                                                                                                                                                                                  
R9    2.2kΩ     RESISTORAXIAL-0.3    AXIAL-0.3      Generic Resistor Package                                                                                                                                                                                                                                                                                                                                                                                  
R10   2.2kΩ     RESISTORAXIAL-0.3    AXIAL-0.3      Generic Resistor Package                                                                                                                                                                                                                                                                                                                                                                                  
R11   2.2kΩ     RESISTORAXIAL-0.3    AXIAL-0.3      Generic Resistor Package                                                                                                                                                                                                                                                                                                                                                                                  
R12   2.2kΩ     RESISTORAXIAL-0.3    AXIAL-0.3      Generic Resistor Package                                                                                                                                                                                                                                                                                                                                                                                  
R13   2.2kΩ     RESISTORAXIAL-0.3    AXIAL-0.3      Generic Resistor Package                                                                                                                                                                                                                                                                                                                                                                                  
R14   2.2kΩ     RESISTORAXIAL-0.3    AXIAL-0.3      Generic Resistor Package                                                                                                                                                                                                                                                                                                                                                                                  
RELAY 4-PIN     MA04-1               MA04-1         PIN HEADER                                                                                                                                                                                                                                                                                                                                                   unknown    unknown   41                      
ROOM  3-PIN     HDR-3                HDR-3_VERT     PIN HEADER                                                                                                                                                                                                                                                                                                                                                                                                
X1    RJ45-8X   RJ45-8X              RJ45-NO-SHIELD CORCOM Modular RJ Jacks No Shield                                                                                                                                                                                                                                                                                                                    RJ45-8X unknown    16R6101   0                       
X2    RJ45-8X   RJ45-8X              RJ45-NO-SHIELD CORCOM Modular RJ Jacks No Shield                                                                                                                                                                                                                                                                                                                    RJ45-8X unknown    16R6101   0                       
X3    RJ45-8X   RJ45-8X              RJ45-NO-SHIELD CORCOM Modular RJ Jacks No Shield                                                                                                                                                                                                                                                                                                                    RJ45-8X unknown    16R6101   0                       
X4    RJ45-8X   RJ45-8X              RJ45-NO-SHIELD CORCOM Modular RJ Jacks No Shield                                                                                                                                                                                                                                                                                                                    RJ45-8X unknown    16R6101   0

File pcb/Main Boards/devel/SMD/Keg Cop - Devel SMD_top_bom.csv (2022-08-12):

Comment | Designator | Footprint | LCSC Part #
0.1µF | C1 C3 | SMD-0805 | C28233
1.0µF | C2 C4 | SMD-0805 | C28323
2k2½ | R1 R2 R3 R4 R5 R6 R7 R8 R9 R12 R13 R14 R15 R16 | SMD-0805 | C17518
60.4½ | R10 R11 | SMD-0805 | C25323
DS18B20Z | KEG LOWER ROOM TOWER UPPER | SOIC127P600X175-8N | C695837
LED_0603LED_SMD_0603 | COOL SOLENOID | LED_SMD_0603 | C2286
TS08-66-43-BK-160-SMT-67 | FLOW0 FLOW1 FLOW2 FLOW3 FLOW4 FLOW5 FLOW6 FLOW7 FLOW8 | SW_TS08-66-43-BK-160-SMT-67 | C2889023

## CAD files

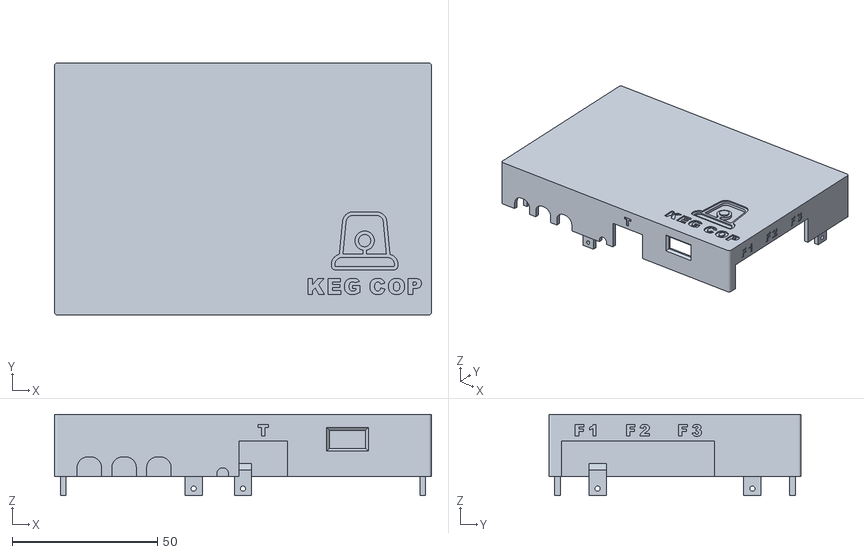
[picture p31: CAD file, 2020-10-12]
case/Main Boards/Main Enclosure - Top.stl
130.0 x 87.0 x 28.0

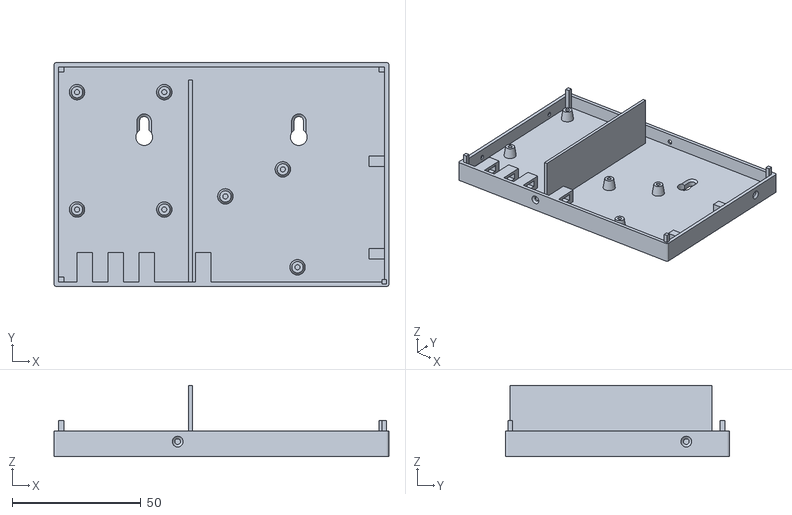
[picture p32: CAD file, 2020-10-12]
case/Main Boards/Main Enclosure - Bottom.stl
130.0 x 87.0 x 27.6

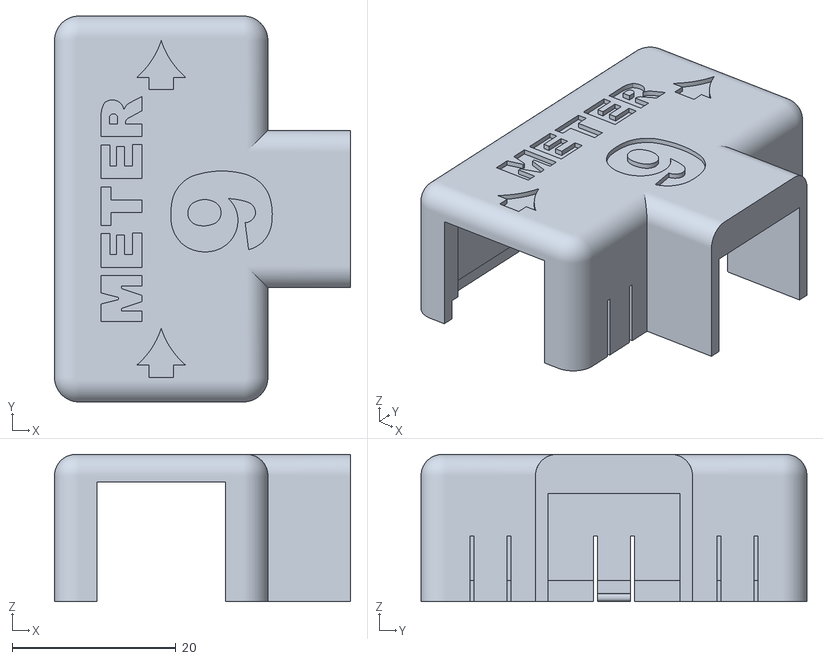
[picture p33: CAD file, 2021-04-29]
case/Breakouts/Daisy Chain/DaisyChainCase_9.stl
36.2 x 47.2 x 18.0

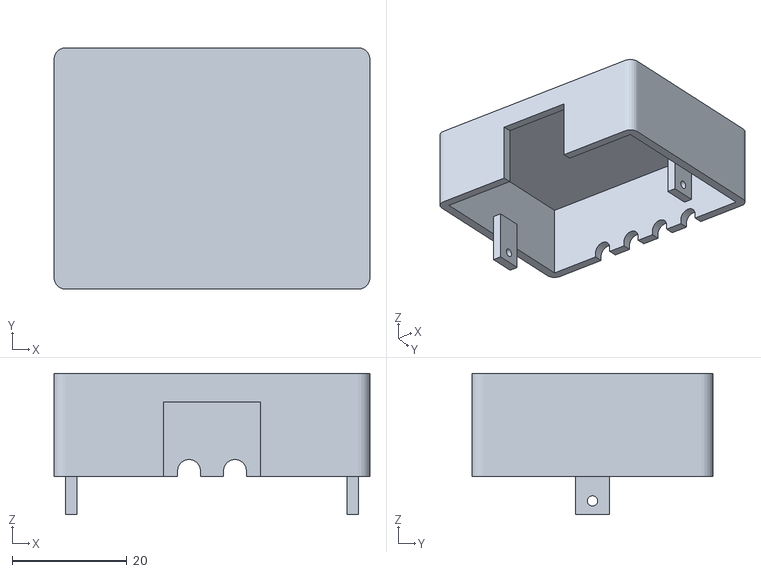
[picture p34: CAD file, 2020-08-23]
case/Breakouts/Temp Sensor/Sensor Board Enclosure - Top.stl
55.0 x 42.0 x 24.6

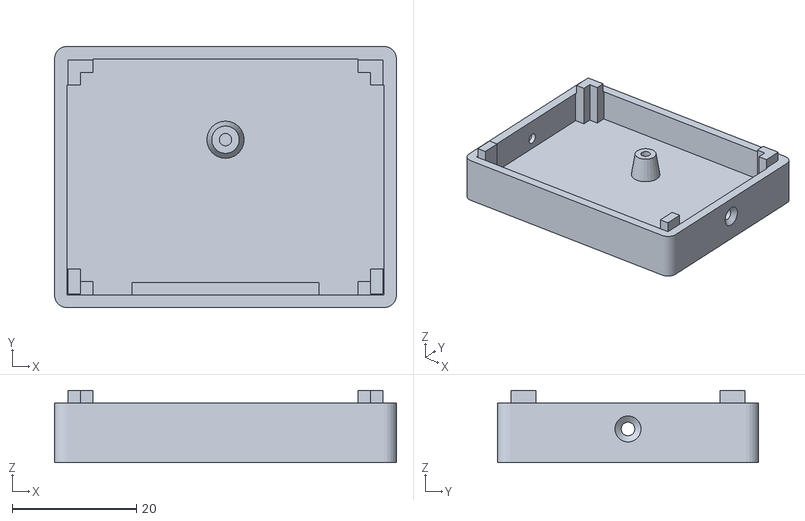
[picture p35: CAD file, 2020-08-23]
case/Breakouts/Temp Sensor/Sensor Board Enclosure - Bottom.stl
55.0 x 42.0 x 11.6

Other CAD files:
case/Breakouts/Daisy Chain/DaisyChainCase_5.stl
case/Breakouts/Daisy Chain/DaisyChainCase_2.stl
case/Breakouts/Daisy Chain/DaisyChainCase_6.stl
case/Breakouts/Daisy Chain/DaisyChainCase_3.stl
case/Breakouts/Daisy Chain/DaisyChainCase_4.stl
case/Breakouts/Daisy Chain/DaisyChainCase_1.stl
case/Breakouts/Daisy Chain/DaisyChainCase_8.stl
case/Breakouts/Daisy Chain/DaisyChainCase_7.stl

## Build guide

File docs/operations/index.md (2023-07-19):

(operations)=

# Operations and Configuration

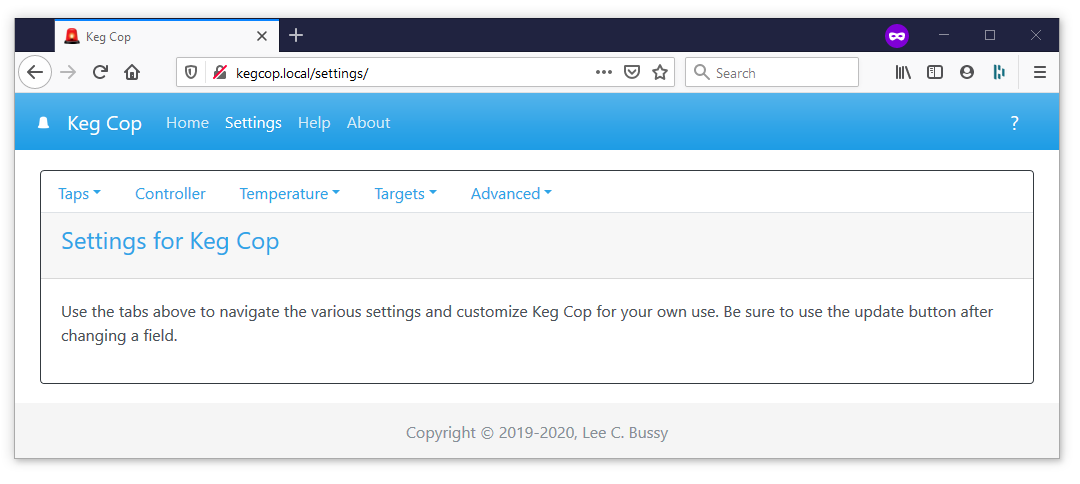
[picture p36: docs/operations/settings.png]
```{image} settings.png
:align: center
:alt: Settings Page
:scale: 60%
```

At a minimum, you will want to look at the settings menu to set up your new device. See the links below for a description of each option.

{ref}`Controller <controller>`:

- Hostname
- Brewery name
- Kegerator/Keezer name
- Units of measure
- Reporting functionality

{ref}`Taps <taps>`:

- Pulses per unit of measure
- Beverage name
- Capacity of keg
- Remaining in keg
- Tap active/inactive

{ref}`Temperature Control <cooling>`:

- Set point
- Control point
- Control enabled/disabled

{ref}`Temperature Sensors <sensors>`;

- Calibration
- Enabled/disabled

Targets:

- {ref}`KegScreen Target <kegscreen>`
- {ref}`Generic REST Endpoint <rest>`
- {ref}`Raspberry Pints Target <rpints>`
- {ref}`Taplist.io <taplistio>`

Advanced

- {ref}`Calibrate flowmeters <calibrate>`
- {ref}`Reset controller <reset>`
- {ref}`Update application <update>`
- {ref}`Reset WiFi <resetwifi>`

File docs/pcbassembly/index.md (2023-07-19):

(pcb)=

# PCB Assembly

Keg Cop runs on an ESP32 controller. To detect the information to be logged, you need to connect specific devices to the controller. I have provided a main circuit board design, as well as several breakouts for your use.

Assembly is not difficult, but it does require some basic soldering.

## Materials Required

This project uses widely-available and inexpensive components. You may find you are better off buying a resistor assortment, for instance, or buying 10 or 20 of a piece at a time for a nominal cost from China.  You will need to order the printed circuit boards from a supply house. The heart of the system is, of course, the controller.

Because there are multiple ways to configure this Keg Cop system, I will demonstrate using my single Kegerator, three taps, and a temperature control setup. Other configurations may be detailed on the {ref}`planning <planning>` page.

Gather the following parts and pieces to get started:

### Controller

The ESP32 controller is paired with many different "developer boards" to make connections easier. While you can buy a bare ESP32 chip, you will walk that road alone.

The developer board used in this project is the Lolin D32 v1.0.0 (not the Pro or 2.0.) Wherever you purchase it, make sure it is an official Espressif ESP32-WROOM-32 Module. It says 4MB (or sometimes shown as 32Mb, which is 4 megaBYTES converted to megaBITS.)  There is a version sometimes called "LED," which means there is an annoying blinking LED when a battery is not connected.  It will work, and so long as it's in a case, you won't notice the blinking.  Be sure it comes with the 16-pin male and female headers, or get them elsewhere. It is common to only receive the male headers in the package.

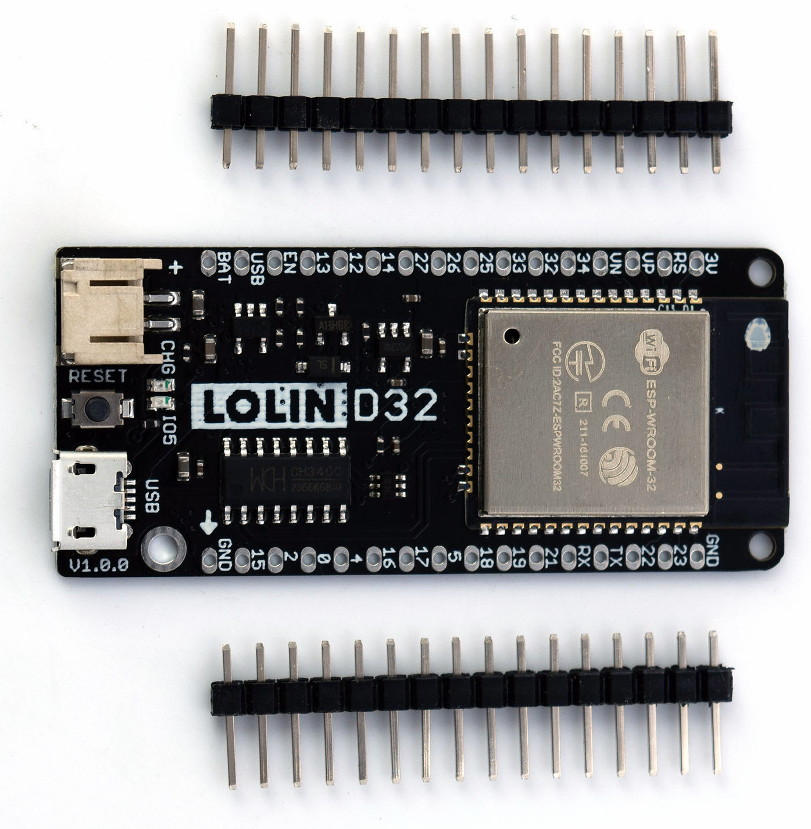
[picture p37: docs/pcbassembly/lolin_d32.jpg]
```{image} lolin_d32.jpg
:align: center
:alt: Lolin D32 v1.0.0
:scale: 50%
```

You can find the Lolin D32 in many places.  Lolin D32 is one of maybe hundreds of development boards. Their prime delivery method to hobbyists seems to be [the Lolin store on AliExpress](https://www.aliexpress.com/item/32808551116.html).

AliExpress also seems to be the least expensive path, but of course, ordering direct from China does take a bit longer than other methods.  You will spend more but get your hands on the device quicker if you purchase from [Amazon](https://www.amazon.com/Genuine-Original-LOLIN-D32-V2-0-0/dp/B07T1SCXYW) or any other place you can find it.

### Printed Circuit Boards

This configuration will use the following three boards:

- [Main Board](https://oshpark.com/shared_projects/UQZn4ng4)
- [Sensor board](https://oshpark.com/shared_projects/MkSWgv0t)
- 3 x [Daisy Chain boards](https://oshpark.com/shared_projects/Zc4zPNjI)

The links will take you to OshPark where I have uploaded the designs.  OshPark is not the cheapest, but they are the most consistent fab house I have dealt with.  You're only talking the difference of a few dollars in your project between them and other fab houses.  For my peace of mind, and for me to recommend them to you, I think it's worth it.  You may take the files from GitHub and upload them yourself somewhere else to save money if you choose.

### Components

For this configuration, we will use the following components:

**Main Board:**

- 2 x [2.54mm Pitch Single Row Female 16P PCB socket Board Pin Header Connector Strip Pinheader 2/3/4/6/10/12/16/20/40Pin For Arduino](https://www.aliexpress.com/item/1005001418544370.html?algo_exp_id=d7709a47-14ca-46e1-bdcb-fe609affb88a-0) (D32) (Note: Multiple items on the page, be sure to select the proper item)
- 2 x [0.1μF (1.0nF) Ceramic Capacitor (102) 2.54mm spacing](https://www.aliexpress.com/item/32868001945.html) (C1, 3) (Note: The same link as below, select the proper item)
- 2 x [1.0μF Ceramic Capacitor (105) 2.54mm spacing](https://www.aliexpress.com/item/32868001945.html) (C2, C4) (Note: The same link as above, select the proper item)
- \*1 x [DS18B20 PCB-mount sensor](https://www.aliexpress.com/item/1901263688.html) (IC1) (Note: Multiple items on the page, be sure to select the proper item)
- 14 x [2.2kΩ 1/4W 5% Axial Resistor](https://www.aliexpress.com/item/32660635741.html) (R1-R5) (Note: Multiple items on the page, be sure to select the proper item)
- 4 x [RJ45 8-pin 90° no shield PCM-mount jack](https://www.aliexpress.com/item/32736146888.html)
- 1 x [2-pin Straight Male Header](https://www.aliexpress.com/item/2040310671.html) (POWER) (Note: More than enough in one lot for all three headers)
- \*1 x [3-pin Straight Male Header](https://www.aliexpress.com/item/2040310671.html) (ROOM) (Note: More than enough in one lot for all three headers)
- 1 x [4-pin Straight Male Header](https://www.aliexpress.com/item/2040310671.html) (RELAY) (Note: More than enough in one lot for all three headers)

If you want the convenience of one-click ordering from the US, the BOM for the main board parts (not the PCB itself) may be purchased from [Mouser](https://www.mouser.com/ProjectManager/ProjectDetail.aspx?AccessID=7085525c8d).  This does not include the DS18B20 temperature sensor.

**Sensor Board:**

- 1 x [RJ45 8-pin 90° no shield PCM-mount jack](https://www.aliexpress.com/item/32736146888.html)
- 4 x [3-pin terminal block](https://www.aliexpress.com/item/32965348107.html)
- \*4 x [DS1820 Stainless steel package Waterproof DS18b20 temperature probe](https://www.aliexpress.com/item/4000895660165.html?algo_exp_id=4e52347a-1295-44ca-8766-1ef0f244c1d2-1) (Note: Multiple items on the page, be sure to select the proper item)

If you want the convenience of one-click ordering from the US, the BOM for the sensor board (not the PCB itself) may be purchased from [Mouser](https://www.mouser.com/ProjectManager/ProjectDetail.aspx?AccessID=db4e1f22c9).  This does not include the DS18B20 temperature sensors.

**Daisy Chain Boards (per flowmeter, multiply all numbers x 3 for three flowmeters):**

- 2 x [RJ45 8-pin 90° no shield PCM-mount jack](https://www.aliexpress.com/item/32736146888.html)
- 1 x [3-pin terminal block](https://www.aliexpress.com/item/32965348107.html)

If you want the convenience of one-click ordering from the US, the BOM for the daisy-chain board (not the PCB itself) may be purchased from [Mouser](https://www.mouser.com/ProjectManager/ProjectDetail.aspx?AccessID=92f043e4f8).  You will need one of this list per flowmeter.

(\*) - Optional items for use when you desire a room temperature sensor. Either use a DS18B20 sensor with a lead or a PCB-mount sensor - the sensor on a lead is recommended to avoid invalid readings due to heat from the controller.

### Soldering

You are going to have to solder.  If you have legitimately never soldered anything before, I recommend you spend a few minutes on YouTube and watch a few videos.  [Sparkfun](https://learn.sparkfun.com/) also has a very nice [tutorial](https://learn.sparkfun.com/tutorials/how-to-solder-through-hole-soldering). It is not hard at all once you get the hang of it.  And, while the boards are comparatively small, the components chosen are simple through-hole parts, which may be easily soldered by a beginner with a little patience.

Be sure to use flux when you solder. Liquid flux is the easiest to use. Be sure to get both sides of the board because you want the solder to flow to both sides.  After you solder from behind, flip the board over to make sure you get a good flow. If not, you can always touch up from the top (but don't tell anyone you cheated.)

I do not intend to provide a step-by-step on how to solder here. Still, I recommend the following part installation order for ease of assembly:

- Resistors - These are the shortest mounted components. Soldering the resistors to the board first is the least challenging. They are also some of the most heat-tolerant parts, so these grant you some experience to get you going.
- Capacitors - The next tallest components, these should go on next. They are also relatively tolerant of heat, so you can continue to refine your skills. Be sure to get them as close to the board as possible since having them stick up changes their intended impact on the circuit.
- DS18B20 Sensor - Now that you are sure of your skills, this sensor should be soldered next if you use one. Be careful not to overheat the device, but they are not too sensitive.
- Pin headers and terminal blocks - These components are not vulnerable to the heat at all except for the plastic.
- RJ45 Jacks - These are the tallest items, and you should solder them on last.

When you solder the sensor board, you have a choice. I designed it to orient the 3-pin terminal block's openings pointing *in* to route the cables together out one end of a case. You may reverse them if you prefer.

Once you have finished soldering the shield, make sure to clean off the flux. You can use cheap vodka or Everclear, or a commercially available flux solvent.

## Modifications

The [pcb directory](https://github.com/lbussy/keg-cop/tree/master/pcb) in the repository contains the Eagle files for the printed circuit board shield supporting Keg Cop.  You can download the design files, modify them, and upload them to the PCB manufacturer of your choice.  If you would like to personalize these board designs, you may edit them with Autodesk's EAGLE. EAGLE is a scriptable electronic design automation (EDA) application with schematic capture, printed circuit board (PCB) layout, auto-router, and computer-aided manufacturing (CAM) features. EAGLE stands for Easily Applicable Graphical Layout Editor and is developed by CadSoft Computer GmbH.

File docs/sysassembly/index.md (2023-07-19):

(assembly)=

# System Assembly

As you have learned in the discussion on {ref}`planning your system <planning>`, Keg Cop is capable of a wide variety of configurations. Each has similar building blocks, and you may apply that methodology to a variety of applications.

Described here are a system with two flow meters, a room temp sensor, a keg temp sensor, a chamber sensor, cooling control, and a solenoid.

The main board is the centerpiece of the system. It hosts the controller and serves as a connection for the relay, sensors, and flow meters.

```{image} system.png
:align: center
:alt: System Diagram
:scale: 15%
```

## Power

You will power the system with a micro-USB cable plugged directly into the controller's USB port.

## Flowmeters

In the diagram above, you can see a crucial feature of the system; a single Ethernet cable leads to one or more flowmeters. The first cable is from the main board to the first flowmeter.  Using the Daisy Chain boards, the first connection is always Flowmeter #1.  Any subsequent connections will be #2, #3, and so on up to six.

## Temperature Sensors

Temperature sensors are optional; however, we will use them in this exemplar configuration.

### Room Temperature

The room temperature sensor is optional, and we use it for display/reference purposes only. If you choose to utilize a room-temperature sensor, you have a choice.  Either solder a DS18B20 in a TO-92 package directly to the PCB or using a sensor pre-assembled on a lead.

If you use a TO-92 package sensor, be sure to provide ventilation for the main board. The ESP32 chip will generate some heat and throw off the readings if you do not.

### Chamber Temperature

Keg Cop offers four optional chamber sensors; we will use two for this example.  We will use a single Ethernet cable to connect the Sensor breakout board to the main board.  One pre-wired DS18B20 sensor is used each on the Keg and the Upper sensor ports.

## Relays

This system will control both the cooling and solenoids. We will use two-channel 5VDC relay to provide this control.

Since the controller pins are 3V3 (3.3VCD), we use a separate 5VDC supply to the relay. This power connection is optional but recommended.  Most relays seem to do fine when actuated with 3V3, but two extra wires are incredibly cheap for some peace of mind.

Remove the jumper between JD-VCC and VCC on the relay board.  Connect the two-pin header labeled POWER on the main board in the following manner:

- JD-VCC on the relay to V on POWER header
- GND on the relay to G on POWER header
- NOTE: The VCC pin on the relay's three-pin header remains unused

We will use the four-pin header to control the relays. Connect the four-pin header labeled RELAY on the main board in the following manner:

- VCC on the relay to V on RELAY header
- IN1 on the relay to C on RELAY header
- IN2 on the relay to S on RELAY header
- GND on the relay to G on RELAY header

### Cooling

In this diagram, we use Relay #1 for cooling. This document is not sufficient to describe how to do high voltage wiring. If you are not familiar with this concept, please seek out a licensed and insured electrician.

Generally, we use the is used to make or break the hot side of the high voltage electrical circuit. When used in this manner, run the hot leg to the COM1 terminal. Run the load side to the NO1 terminal.

### Solenoid

Solenoids come in a wide variety of configurations. I have designed this system to actuate a single relay to control one or more solenoids simultaneously. Power the solenoids with a separate, dedicated power supply of sufficient amperage and proper voltage for the relays you implement.  Run them in parallel, through the COM2 and NO2 terminals on Relay #2.

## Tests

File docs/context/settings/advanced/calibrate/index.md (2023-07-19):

(calibrate)=

# Calibrate Flowmeters

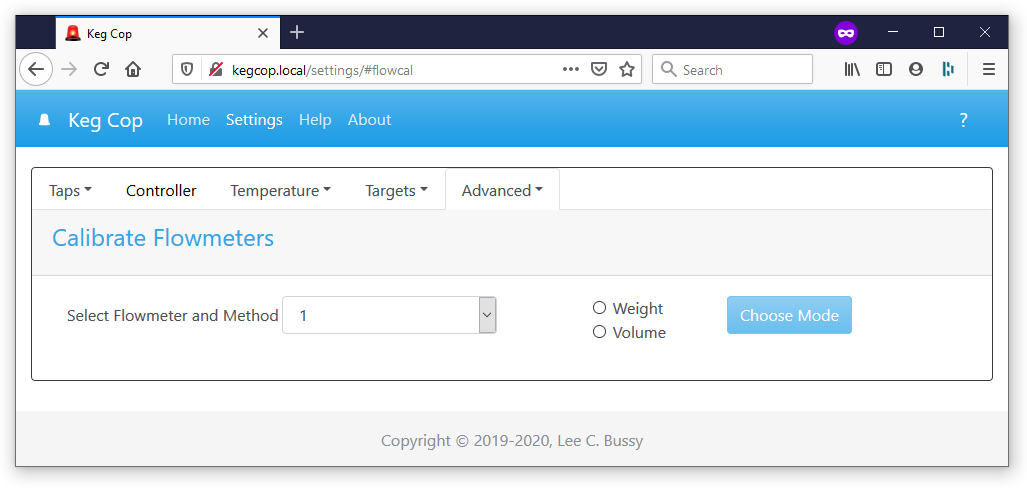
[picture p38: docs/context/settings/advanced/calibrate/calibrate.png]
```{image} calibrate.png
:align: center
:alt: Flowmeter Calibration Screen
:scale: 50%
```

Upon opening the Calibrate Flowmeters page, you are presented with a dropdown to select the flowmeter to be calibrated. After choosing the meter, select a radio button to select between calibrating by a weight or a volume measurement.  The Choose Mode button will activate upon selecting a method. Pressing this button will open an additional dialog, depending upon your choice.

Calibration by volume is often less accurate than weight; however, using volume is the most straightforward method.

## Calibration by Volume

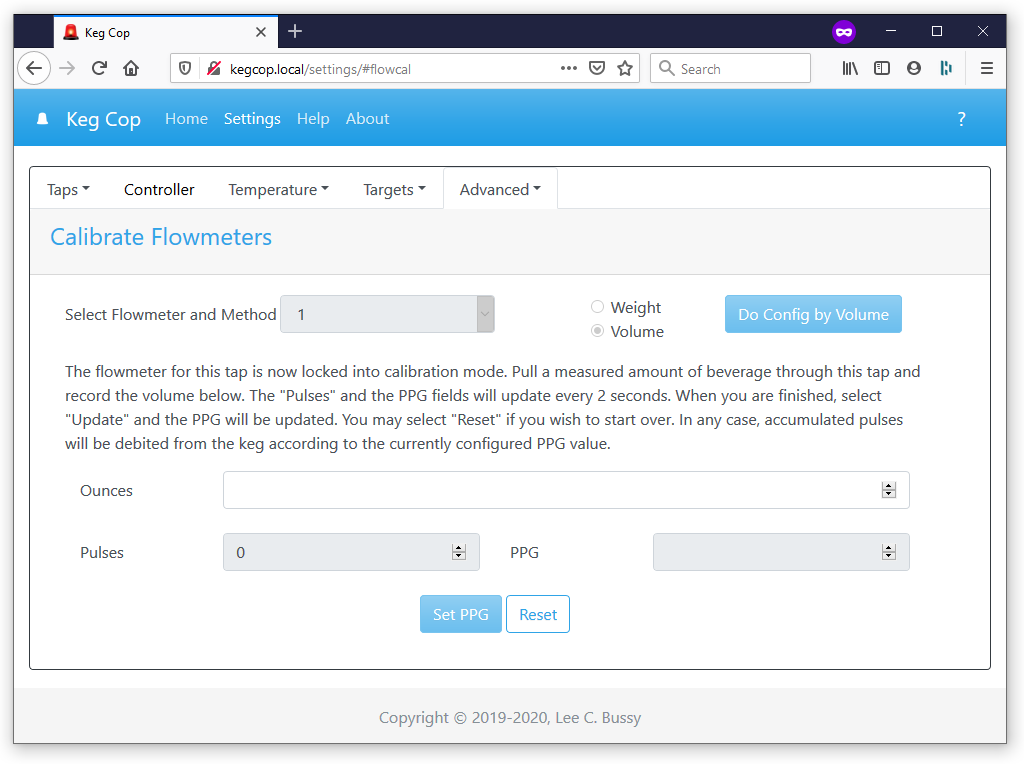
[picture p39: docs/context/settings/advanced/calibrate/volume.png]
```{image} volume.png
:align: center
:alt: Calibration by Volume Screen
:scale: 50%
```

Calibration by volume involves measuring a tap pull of a beverage and then recording that measurement. A larger pour will be more accurate than a smaller one. Enter volume measurements in the units for which you have configured Keg Cop. Use milliliters if using metric, or ounces if using imperial measurements.

As you draw a beverage during calibration, the Pulses field will update with the pulses measured. If you have entered a volume, the pulses per unit (PPG or PPL) are calculated. Both the Pulses and pulses per unit will update every two seconds.

When you are satisfied, use the Set PPG/PPL button to lock in the calibration. If you wish to reset the calculation back to its default, use the Reset button instead of saving. The pulses collected will be debited according to the new rate if you save, or the previously configured rate if you reset.

## Calibration by Weight

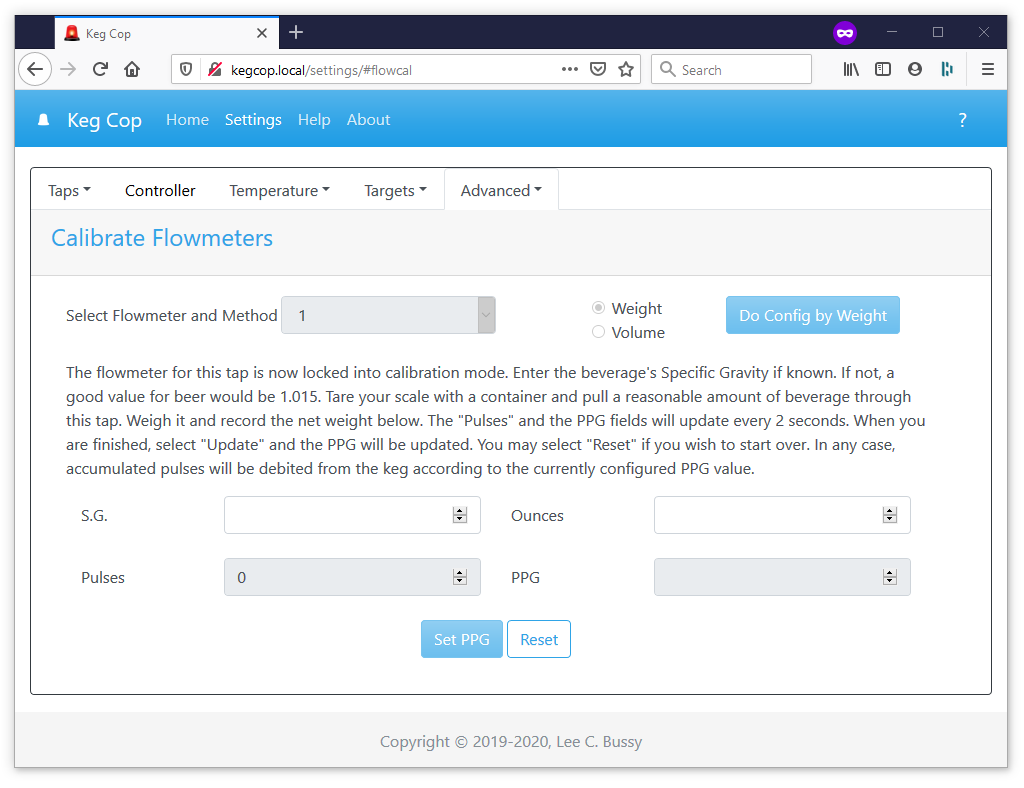
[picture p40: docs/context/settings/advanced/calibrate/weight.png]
```{image} weight.png
:align: center
:alt: Calibration by Weight Screen
:scale: 50%
```

Since some beverages may have a specific gravity other than 1.000, and we measure by volume, adjustment of the measure taking into account the SG is possible.  If you are unsure of what to use, 1.015 is a good middle of the road number for most homebrewed beer.  If you leave it blank, the calibration employs 1.000 (water equivalence).

Tare your scale with the container you will be using. Pull an amount of beverage roughly equivalent to a standard pour. Weigh the container again to determine the net weight. Use the units of measure appropriate for the current Keg Cop configuration; use ounces for imperial and grams for metric.

As you draw a beverage during calibration, the Pulses field will update with the pulses measured. If you have entered a weight, the page calculates the pulses per unit (PPG or PPL). Both the pulses and pulses per unit will update every two seconds.

When you are satisfied, use the Set PPG/PPL button to lock in the calibration. If you wish to reset the calculation back to its default, use the Reset button instead of saving. The pulses collected will be debited according to the new rate if you save, or the previously configured rate if you reset.

## Tap Setup

See the {ref}`Taps <taps>` settings page for other tap settings.

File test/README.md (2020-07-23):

Keg Cop Logo Keg Cop (http://www.kegcop.com/)

# Test

This directory is intended for PIO Unit Testing and project tests.

Unit Testing is a software testing method by which individual units of
source code, sets of one or more MCU program modules together with associated
control data, usage procedures, and operating procedures, are tested to
determine whether they are fit for use. Unit testing finds problems early
in the development cycle.

More information about PIO Unit Testing:
- https://docs.platformio.org/page/plus/unit-testing.html

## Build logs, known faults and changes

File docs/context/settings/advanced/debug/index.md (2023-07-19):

(debug)=

# Debug Configuration

Debug Configuration deals with both the verbosity of messages and if Telnet is available.

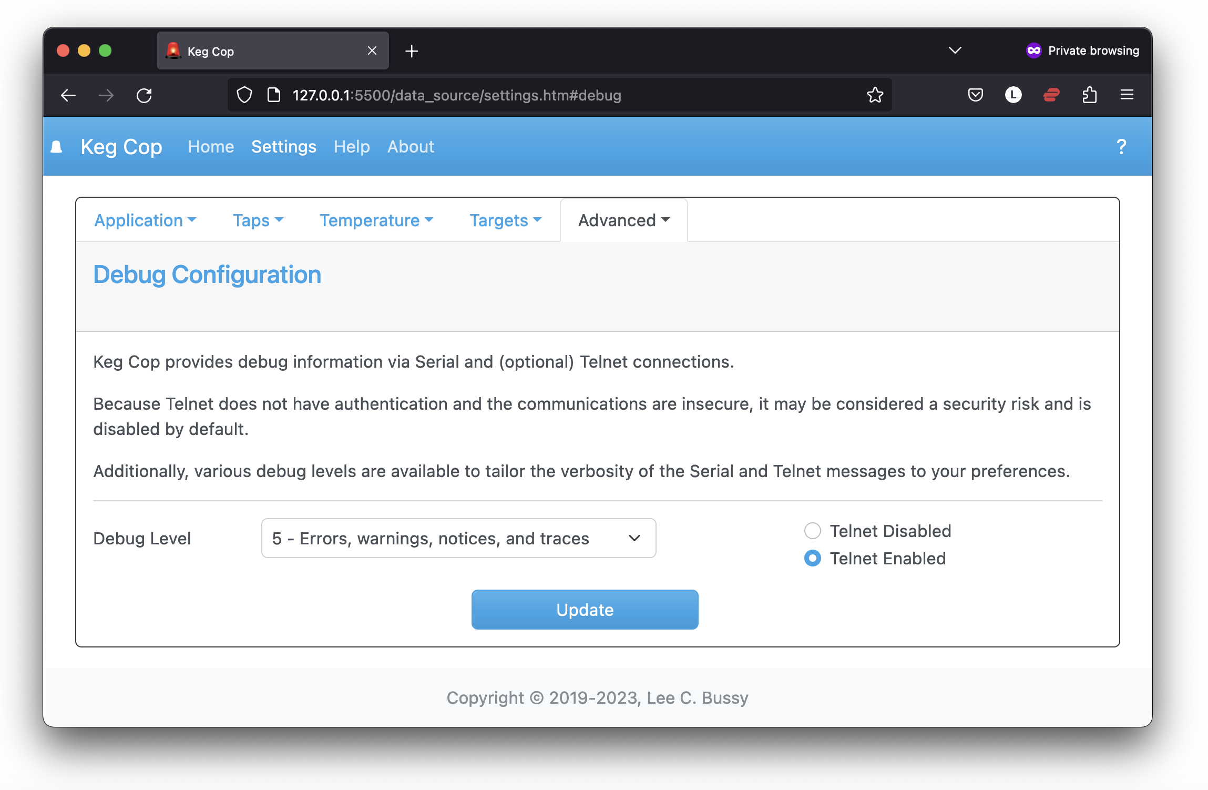
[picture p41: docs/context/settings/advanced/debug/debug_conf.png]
```{image} debug_conf.png
:align: center
:alt: Debug Calibration Screen
:scale: 30%
```

## Log Level

The drop-down shows seven verbosity levels:

0.  `LOG_LEVEL_SILENT`     No logging output is displayed
1.  `LOG_LEVEL_FATAL`      Shows only fatal events
2.  `LOG_LEVEL_ERROR`      Shows errors and fatal events  
3.  `LOG_LEVEL_WARNING`    Shows errors and warnings 
4.  `LOG_LEVEL_NOTICE`     Shows errors, warnings, and notices 
5.  `LOG_LEVEL_TRACE`      Shows errors, warnings, notices, and traces 
6.  `LOG_LEVEL_VERBOSE`    Shows all log output

Higher logging levels are helpful for debugging tasks.  There is no performance impact from the various levels.  Serial logging is enabled by default, and you may connect with a micro USB *data* cable to your computer.  The baud rate is 115200, and the connected controller is easily powered through this cable.

## Telnet

Telnet is a valuable tool when debugging or monitoring is required, and the system is in a place where connecting a serial cable is impractical.  You may connect to the controller via port 23; no authentication is required.  Because this can present a security risk in some environments, this is disabled by default.

Never open your controller, either the web UI or Telnet, to the Internet.

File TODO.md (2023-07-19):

# TODO

- [ ] Enter keg contents by weight

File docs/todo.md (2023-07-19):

(todo)=

# Documentation TODOs

```{eval-rst}
.. todolist::
```

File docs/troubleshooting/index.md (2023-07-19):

(troubleshooting)=

# Troubleshooting

This section will grow over time.  I will add things here representing items that more commonly trip people up.

## Backup and Restore

I have created a filesystem UI to use should you desire to back up or restore your configuration.  You may find this by navigating to `http://{hostname}.local/edit` (or via the IP address.)

```{image} filesystem_info.png
:align: center
:alt: Filesystem Editor
:scale: 30%
```

:::{note}
The username is `admin`, and the password is `p@ssword`.
:::

Here you can:

- `List Files` on the controller filesystem, or;
- `Upload File` to the filesystem

If you upload a file of the same name, the tool will overwrite the original without confirmation.

The two configuration files are:

- `appconfig.json` - Contains configuration for the controller and the UI
- `flowconfig.json` - Contains information about your taps and tapped kegs

If you upload a configuration file, you must immediately reset the controller via the reset button (or a power cycle.)  If you wait or use the controller reset functionality in the UI, the system will overwrite your uploaded configuration with the original.

If the JSON is incomplete, the system will revert to default settings.  If there are extra fields, the system will delete them.  If the JSON is invalid, the application will write a new default configuration in its place.  Be sure you check your JSON format before you upload.

(faq-mdns)=
## Cannot open Keg Cop by Name

- Windows requires [Bonjour Print Services for Windows](https://support.apple.com/kb/DL999?locale=en_US) to be installed to find local devices by name.  Technically, newer OS versions and patch levels have mDNS support; however, that is only for 64-bit applications.  Most web browsers are 32-bit.
- If you are on Windows 10 and still have issues, see the article: [Disable Windows mDNS](https://superuser.com/questions/1330027/how-to-enable-mdns-on-windows-10-build-17134)
- On Windows, to check if mDNS is working properly (independent of connecting to the controller), you can use [Bonjour Browser](https://hobbyistsoftware.com/bonjourbrowser)

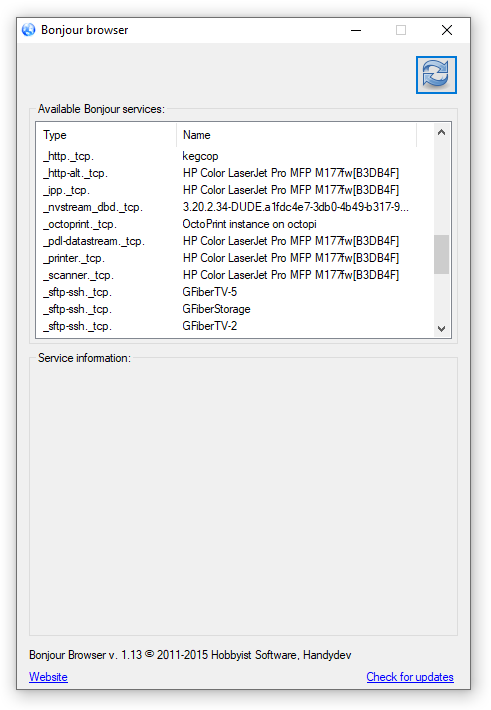
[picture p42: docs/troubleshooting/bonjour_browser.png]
```{image} bonjour_browser.png
:align: center
:alt: Controller Settings
:scale: 50%
```

- Android phones have had a questionable history of support for mDNS - likely because the technology was adopted early on by Apple and is heavily ingrained in the Apple ecosystem.  Reportedly, under ChromeOS 80, the Chrome Browser *does* resolve mDNS names (.local).  Under Android 10, it does not.  There is an issue on the [Issue Tracker](https://issuetracker.google.com/issues/140786115), which is an interesting mix of phanbois giving reasons why it should not be supported, and real users who want it.
- From an Android smartphone, you can use something like [Service Browser](https://play.google.com/store/apps/details?id=com.druk.servicebrowser) to browse mDNS services on your local network.

## MQTT Troubleshooting

Keg Cop has two publish-only MQTT configurations:

- Raspberry Pints: A pulse publication only to the legacy Raspberry Pints system
- Home Assistance: A more generic MQTT publication tested against Home Assistant

It may be helpful to do troubleshooting when problems arise with these systems.  Setting up an MQTT broker is a valuable step.  To set up a broker on a Raspberry Pi (or other Debian-based systems), use the following steps:

1.  Install Mosqitto MQTT broker and pub/sub client: `sudo apt install mosquitto mosquitto-clients`
1.  Check status: `sudo systemctl status mosquitto` (it should show "running")
1.  Add local listener configurations
    1.  Edit the configuration file: `sudo nano /etc/mosquitto/mosquitto.conf`
    1.  Add two lines to the end of the file:
        1.  `listener 1883`
        1.  `allow_anonymous true`
    1.  Restart MQTT: `sudo systemctl restart mosquitto`
    1.  Validate your change to make sure it is running `sudo systemctl status mosquitto`
1.  Test the installation:
    1. Subscribe to all: `mosquitto_sub -h localhost -t "#" &`
    1.  Send a test: `mosquitto_pub -h localhost -t "mqtt/test" -m "Hello world"`
- Optionally, install mosquitto-clients on another system and send a test pub: `mosquitto_pub -h {hostname.local} -t "mqtt/test" -m "Hello world"`

You may now set up either publication service and receive and review reports on your testing MQTT broker.

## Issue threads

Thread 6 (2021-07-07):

Incorrect copyright date

thorrak, 2021-07-07:
https://github.com/lbussy/keg-cop/blob/401cf2c7e76c4b54fadf538f9cc6c7594caab9e6/data/index.htm#L109

excuse me while I go cry about the implication.

lbussy, 2021-07-07:
I need to figure out how to dynamically set those repetitive strings.

thorrak, 2021-07-07:
Let me know if you figure it out. Seems like it would require either setting a "common string JSON endpoint" or parsing the HTML on its way out of the device. :(

lbussy, 2021-07-07:
There is a way to do some string replacement in the asynch web server.  I'm just not sure what fresh hell it would dredge up.

lbussy, 2021-07-09:
Pushed to `devel`, closing.

Closed 2021-07-09.

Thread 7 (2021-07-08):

Internal & External Tap IDs don't match

thorrak, 2021-07-08:
The internal tap IDs (0-8) and the tap IDs as displayed in the interface (1-9) don't match

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

thorrak, 2021-07-08:
The issue with this is that KegScreen tracks/presents the internal tap ID to users which will be off by one vs. the IDs the user would see in the Keg Cop interface.

My preference would be to switch to use the "external" tap ID everywhere (internally) in Keg Cop - but if you want to tag this as "wontfix" I can hardcode the off-by-one shift in the relevant KegScreen screens/functions.

lbussy, 2021-07-08:
What ever happened to separating business and data functions?  😀

lbussy, 2021-07-09:
Not against this but I'm not sure where it will end.  Is it only the hashes that mess you up?  Or is it that `/api/v1/config/taps/` is zero-based?  I'd prefer to leave the "data" in close correlation to the actual internal (zero-based" arrays, but if there are display portions that are causing confusion we can talk about how best to handle that.

My thinking was if someone used KegScreen, they could name them whatever they want.  I could add a "tap name" field I guess to be pushed by KegScreen?

thorrak, 2021-07-09:
As an example -

I currently don’t cache/support updating PPU inside the KegScreen interface. When the user wants to calibrate the sensor/update PPU I link them to the Keg Cop interface’s calibration workflow. Inside KegScreen, the user would see that they are viewing/updating “Keezer - Tap 0” but in the Keg Cop interface they would need to select to calibrate “Tap 1”.

My thought is that the most straightforward/long-lasting fix would be to swap the zero-based index everywhere inside Keg Cop for the one-based index being displayed, but I can also alternatively change the function that generates the tap name to just add 1 to the tap number inside KegScreen.

lbussy, 2021-07-09:
Changing an index in C++ to be 1-based would be a headache waiting to happen.  What do you think about adding a "name" field to the data for the meter?

lbussy, 2021-12-08:
@thorrak did you have an opinion here?

thorrak, 2022-01-16:
I don't have an opinion, other than to lock down _something_. I think I finished the missing pieces of your "external tap ID label" support in #12 , but didn't go through and test it. If that's the route you want to take with this, I'm fine consuming that and having the user refer to that when linking Keg Cop taps to KegScreen taps.

lbussy, 2022-01-16:
Well, let's assume we did till someone tells us it's broken :)

thorrak, 2022-01-16:
> Well, let's assume we did till someone tells us it's broken :)

I MEAN. The someone here is me, soooo....

lbussy, 2022-01-16:
I guess we do need a way to assign them.  They should probably default to `index + 1` and allow them to be set to custom numbers.

lbussy, 2022-06-26:
Does the solution I suggested in #18 solve this too?

thorrak, 2022-06-26:
> Does the solution I suggested in #18 solve this too?

I don't think so. I thought where we landed was that there needed to be some kind of configurable key that existed internal to Keg Cop that would be provided in each of the reports and could be used to link those reports to KegScreen tap IDs. Controller ID + Keg Cop tap ID is fine, but I need a way to either definitively derive the Keg Cop _internal_ tap ID (and controller ID) for providing data back to Keg Cop from KegScreen or have some kind of key that KegScreen can provide that will let Keg Cop do the derivation.

lbussy, 2022-07-03:
I'm calling this fixed with `taps[n].label`.  You good with that?

``` json
{
  "imperial": true,
  "taps": [
    {
      "tapid": 0,
      "label": 1,
      "pin": 4,
      "ppu": 21120,
      "name": "Pudswiller Doors",
      "capacity": 5,
      "remaining": 4.2,
      "taplistioTap": 0,
      "active": true,
      "calibrating": false
    }
```

Closed 2022-07-03.

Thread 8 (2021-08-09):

Context Help for API Not Correct

lbussy, 2021-08-09:
E.g.: https://docs.kegcop.com/en/latest/context/settings/temperature/api/v1/info/sensors/index.html

lbussy, 2021-12-08:
Apparently the dude running this place is asleep at the wheel!

Closed 2022-01-16.

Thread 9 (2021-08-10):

Temp Calibration Ineffective

lbussy, 2021-08-10:
Temperature calibration does not seem to apply.

lbussy, 2022-06-26:
I fixed this ... somewhere. :)

Anyway, it works in `devel`.

Closed 2022-06-26.

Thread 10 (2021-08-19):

Unable to change setpoint when in Celcius

lbussy, 2021-08-19:
Chamber setpoint changes work in F, not in C.  Reported in [this post](https://www.homebrewtalk.com/threads/keg-cop-keg-monitoring-and-control.692880/post-9148700).

lbussy, 2021-12-08:
.. reminding myself to check on this.  I thought it was fixed.

Closed 2022-01-16.

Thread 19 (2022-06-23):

Allow Invert of Cooling Pin

austinpe, 2022-06-23:
Currently the cooling only works when wired Normally Open (it says so in the docs to do this 😄).

However, some people don't feel comfortable building their own high voltage relays so opt for off-the-shelf products (e.g. powerswitch tail from adafruit or the IoT Relay from Digital Loggers).

As such, it would be nice to allow inverting the Cooling signal to be wired as Normally Closed.

Looking at code, I think it's as simple as turning the HIGH/LOW argument of the digitalWrite function into a variable within the thermostat.cpp.

I'll try to do this update myself and submit a pull request.

Thoughts?

lbussy, 2022-06-23:
Hi Austin.  I don't have an issue with this in theory.  I looked at the device you are talking about and it looks like it's configurable.  Is that not the case?

My only concern here is if you have a failure of the controller, your cooling system will stay on.

lbussy, 2022-06-23:
Notes for myself; pin state is set in (devel):

https://github.com/lbussy/keg-cop/blob/5b3bd46a5df5442c4f9e612c788a3069c134fb5a/src/main.cpp#L78
https://github.com/lbussy/keg-cop/blob/5b3bd46a5df5442c4f9e612c788a3069c134fb5a/src/thermostat.cpp#L51
https://github.com/lbussy/keg-cop/blob/5b3bd46a5df5442c4f9e612c788a3069c134fb5a/src/thermostat.cpp#L80
https://github.com/lbussy/keg-cop/blob/5b3bd46a5df5442c4f9e612c788a3069c134fb5a/src/thermostat.cpp#L105

lbussy, 2022-06-23:
Added `config.temps.coolonhigh` in the json.

austinpe, 2022-06-23:
You are correct that the device is configurable, but the layout is not.
For example, on the IoT Relay if you plug into the NO socket then you block the 'Always On' socket.
Not really your project's problem, but part of my motivation for the request!

And yes, using the Normally Closed relay would result in a 'failing closed' situation if the controller failed and you'd be cooling when you shouldn't be. I think this may actually be a preferred result for some, though.

For example, the chest freezer I use for my keezer has a dial that allows the user to set how cold/'hot' they want the chest freezer to be by default. I have it turned all the way up such that without any temp control device the freezer barely gets below freezing (but still too cold for beer 😄). The keezer is in my garage, so on a hot summer day if the controller fails open and I don't notice it I'd rather open the top up and let it 'warm up' ~10 °F than wait for it to cool down by ~10 °F.

lbussy, 2022-06-23:
I get ya.  Okay, I mean this is will be a "change at your own risk" setting of course.  I have it coded, I just need to add a web page form field and a handler for it.

lbussy, 2022-06-23:
Added a POST handler:

``` CPP
            if (strcmp(name, "coolonhigh") == 0) // Enable cooling on pin high (reverse)
            {
                if (strcmp(value, "true") == 0)
                {
                    Log.notice(F("Settings update, [%s]:(%s) applied." CR), name, value);
                    config.temps.coolonhigh = true;
                }
                else if (strcmp(value, "false") == 0)
                {
                    Log.notice(F("Settings update, [%s]:(%s) applied." CR), name, value);
                    config.temps.coolonhigh = false;
                }
                else
                {
                    Log.warning(F("Settings update error, [%s]:(%s) not valid." CR), name, value);
                }
            }
```

lbussy, 2022-06-23:
Okay, @austinpe: I don't have a testbed where I am right now, but I have created a `cool_state` branch which should do what you need.  Please let me know how it works for you.

austinpe, 2022-06-23:
awesome! I'll test it within the next few hours.
Is it possible for me to do an OTA with the new firmware in that branch? Or will I need to flash it manually?

lbussy, 2022-06-23:
You would have to do it manually, via PlatformIO if you have it.  If not, I can try to put it up on BrewFlasher for you.

lbussy, 2022-06-23:
It's in BrewFlasher.  You can use the app, or [BrewFlasher Web](https://web.brewflasher.com/):

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

austinpe, 2022-06-23:
The webapp didn't have an error message, but it "flashed" much too fast to be real:

Serial Out shows it's in a bootloop, just keeps repeating this message:

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

In BrewFlasher standalone:
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

I see you put the firmware in the branch. I'll flash manually with esptool.py

lbussy, 2022-06-23:
Just now (18:14 CT) I pushed a new firmware. I am not sure but I think I may have uploaded the wrong one. Try again if you already flashed the other version.

austinpe, 2022-06-23:
I grabbed the latest firmware from the repo.
I cleared the esp32 first.
I flashed the partition, firmware, and spiffs manually with esptool.py to the correct address according to the docs.

There's a different bootloop now:

> rst:0x10 (RTCWDT_RTC_RESET),boot:0x13 (SPI_FAST_FLASH_BOOT)
> flash read err, 1000
> ets_main.c 371

Not sure if you updated BrewFlasher but it still says there's an error with downloading the partitions file.

lbussy, 2022-06-23:
Grrr ... sorry about that. I need to find an ESP32 here somewhere to try this on.  Will be morning (not sure where you are, about 12 hours from now) before I can get to it.  The changes were simple enough that I didn't expect a crash.

austinpe, 2022-06-24:
Absolutely no problem.
Thank you for your time and energy on this it's beyond appreciated.
I'm east coast US, btw.

If there's a clear starting point you see I can poke around tonight.
I've used PlatformIO before so can compile the source myself, but I would not say I'm fluent in C++... enough to be dangerous.

lbussy, 2022-06-24:
My next step would be to compile in debug mode and use the exception decoder to figure out where it's crashing.  It's never straightforward. :)

austinpe, 2022-06-24:
100% -- and I'm happy to help test/code.
I actually commented on the Fermentrack thread on HBT (I'm 'Feynman' over there) saying that I was excited about that feature.

I actually had my own make-shift Kasa setup. I monitored the cooling signal using an always-running python script and used it to turn on/off the Kasa plug. But it just wasn't sustainable.

The risk I've found from the Kasa plug strategy is that if there's a power surge or random network outage then it's really hard to have robust recovery code that handles all cases. Whereas a hardwired setup can survive network outages.

lbussy, 2022-06-24:
Ultimately, it's going to be up to the end-user to come up with a robust networking strategy and that may include some work around the order by which things recover in case of an outage.  I know I have to do that myself (and Kasa plugs are part of that.)  IFTTT is one way a person can do it.

austinpe, 2022-06-24:
oh for sure, I agree.
But either way, yes, I think it would be a great option to have and I'm happy to help with it.

lbussy, 2022-06-24:
Okay, I seem to have broken BrewFlasher with my update.  Till Thorrak has a chance to tell me what I did wrong, you can download the firmware here:

[**1.0.1-Alpha.1 Allow Inverted Cooling Pin**](https://github.com/lbussy/keg-cop/releases/tag/1.0.1-Alpha.1)
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
lbussy, 2022-06-24:
> It seems that the invert works! I'll keep monitoring.

I approve of this message.

> By the way, did the deadband range for turning on/off the cooling change? Maybe it's just because I'm watching it, but it feels like it's cycling more often? There's no 'short delay' implemented now is there? Again, probably just because I'm actively watching it.

I didn't mess with that part - I'll have a look.

> It seems like the ability to update the taps is broken. I can select a tap and fill in the form, but clicking on 'update' does nothing.
Update: I can successfully update the tap info via API

I think I know what that is.  I blame @thorrak for it.  Labels or something.  I'll take another look at that part.

austinpe, 2022-06-24:
AH! Yes, so I went back via the web interface and put a number into the 'Tap Label' and now it updates.
There's a 'placeholder' value of 1 so I thought it was already filled in when I tried it earlier.

This is what it looks like as the page loads. The 'Tap Label' value is not populated and it's just a placeholder value.:
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

So, even after the tap label is set once, it doesn't populate in on refresh so you can't make changes until you enter something again.

lbussy, 2022-06-24:
> There's a 'placeholder' value of 1 so I thought it was already filled in when I tried it earlier.

Yep, there's still a bug on my side.  I need to fix that.

austinpe, 2022-06-24:
Regarding the cycling time, it looks like the
COOLDELAY variable is the same between branches.

However:

```
// Cooling Delay - Default 5 mins (in millis())
//
#ifndef COOLDELAY
#define COOLDELAY 2 * 60 * 1000
#endif
```

It's set to 2 minutes instead of 5 minutes 😄

lbussy, 2022-06-24:
Heh, I wonder what I was thinking there.

You beat me to it, I was going to compare that after I finished re-re-re-fixing my build script.

I can set those back to the initial values here in a moment and give you Alpha.2.

lbussy, 2022-06-24:
BrewFlasher is still broken, you can update with the firmware here:

[1.0.1-Alpha.2 Allow Inverted Cooling Pin (Cleanup)](https://github.com/lbussy/keg-cop/releases/tag/1.0.1-Alpha.2)

To recap:
* In theory I have not broken the cooling pin inversion logic
* I fixed tap labels (which also fixed #20)
* I reverted some changes to the min cool time as well as delay

You should be able to verify the version in the "About" page.

Let me know!

austinpe, 2022-06-24:
> - In theory I have not broken the cooling pin inversion logic

✔️
> - I fixed tap labels

✔️
> - which also fixed https://github.com/lbussy/keg-cop/issues/20

❌ -- I put a comment in that bug
> - I reverted some changes to the min cool time as well as delay

✔️

thorrak, 2022-06-24:
> Okay, I seem to have broken BrewFlasher with my update. Till Thorrak has a chance to tell me what I did wrong, you can download the firmware here:

BrewFlasher should be back working now. Sorry about that!

thorrak, 2022-06-25:
> I actually had my own make-shift Kasa setup. I monitored the cooling signal using an always-running python script and used it to turn on/off the Kasa plug. But it just wasn't sustainable. But, I have several Kasa plugs and Kasa strips already that I used for my testing so I'm happy to help if I can!
>
> The risk I've found from the Kasa plug strategy is that if there's a power surge or random network outage then it's really hard to have robust recovery code that handles all cases. Whereas a hardwired setup can survive network outages. I know technically Kasa should be able to communicate via local network even if there's no internet, but I found in my testing that it wasn't dependable.

Were you using the Kasa Cloud or the local ports with your python script? I've had pretty good success with the local ports, but definitely have had devices disappear randomly on the cloud.

The way that I have it working with BrewPi-ESP is to default to failing "off". I'd have to recheck the timings, but every ~5 seconds or so the controller sends a message to the Kasa switch telling it "shut off in 90 seconds". If the network goes out, controller dies, etc. then it has 90 seconds to come back before the Kasa switch shuts off whatever is connected.

austinpe, 2022-06-25:
I was using the [Kasa python library](https://github.com/python-kasa/python-kasa) and directly interacting with the plugs.

I can put my code in a gist if you're interested, but I don't think it's anything too special.

Basically it monitored the faux LCD from Fermentrack (/api/lcd/) to look for the cooling status then syncs that status with the Kasa plug.

lbussy, 2022-06-25:
Don;t mind me - keep talking.  Just closing this issue as it's been moved to `devel`.

Closed 2022-06-25.

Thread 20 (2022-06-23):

Keg Screen 'tapinfo Report' Fails to POST

austinpe, 2022-06-23:
I'm using the Keg Screen functionality as a sort of 'web hook' to allow for reactive updates to an LCD screen instead of constantly polling the API.

I'm mostly using the temp and pour reports for my LCD, but while testing I noticed that the tapinfo report was always failing.

Here's a serial log of what I see. You can see I navigate to the taps page and toggle a tap to be active.
This triggers the tap report POST, but it fails.

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

From my testing the pour, temp, and cooling reports all POST just fine.
I have not tested the kick report.

lbussy, 2022-06-23:
Does it work properly for you when you toggle active/inactive via the normal web interface?

austinpe, 2022-06-23:
This was via the normal web interface.
I have not tried to toggle it via API but I'll try that now.

lbussy, 2022-06-24:
I believe this is also fixed in Alpha.2, give me a few to upload and (pre)release.

austinpe, 2022-06-24:
Sadly I still get the following in the Serial Out when I update a tap.

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

I confirm I still am getting all other reports, just not the tapinfo report.
Here's a successful temp report:

> 2022-06-24T21:36:53Z V: Temps: Preparing POST to: http://192.168.0.27:8080/
> 2022-06-24T21:36:53Z V: Temps POST to http://192.168.0.27:8080/ dispatched.
> 2022-06-24T21:36:53Z N: Temps: HTTP response code 200 received (81ms): Ok.

lbussy, 2022-06-24:
Can you try disabling all browser extensions and/or using private mode?   I can't reproduce that at all.

austinpe, 2022-06-25:
I tested in both an incognito tab with all extensions disabled AND with Postman as a pure API PUT request.

Both times did not trigger a POST received by the listening server. Temp reports are actively being received.

I was not able to listen to the serial out yet.
I tried to flash a 2nd esp32 as a dummy, but it did not let me monitor serial out and use the web page at the same time?
If I had the webpage loaded and opened PuTTY it would show that it caused a panic? Weird. I'll investigate that more later.

lbussy, 2022-06-25:
OH!  I'm sorry I was being dense.  Now I get it.  I'll need to test that again.

lbussy, 2022-06-25:
Just dropping notes here.  I tested with brewpi (`brewpi-api.php`) and I was able to receive the JSON:

```
2022-06-25 07:06:24  Received JSON: {"api":"Keg Cop","guid":"0EF7C6300000XXXX","hostname":"kegcop","breweryname":"Silver Fox Brewery","kegeratorname":"Keezer","reporttype":"tempreport","imperial":true,"controlpoint":4,"setting":35,"status":6,"controlenabled":true,"sensors":[{"name":"Room","value":-196.6000061,"enabled":true},{"name":"Tower","value":-196.6000061,"enabled":true},{"name":"Upper Chamber","value":-196.6000061,"enabled":true},{"name":"Lower Chamber","value":-196.6000061,"enabled":true},{"name":"Keg","value":-196.6000061,"enabled":true}]}
```

I did also receive the error on the terminal:

```
2022-06-25T12:22:17Z W: Warning: Previous transaction for Taps POST is in an unknown state (0).
```

So, I'm with you so far.  All of this would be unnecessary if @thorrak would get Keg Screen done.  😉

Anyway now I know what you are seeing.  I'll poke at it.

austinpe, 2022-06-25:
@thorrak , as side note / plug, I see you've been using Vue on your webapps. I'm a Vue dev and happy to help or test if ya need it.

lbussy, 2022-06-25:
>> I see you've been using Vue on your webapps.

"Using."  It's using him.  😃

thorrak, 2022-06-25:
> > I see you've been using Vue on your webapps.
>
> "Using." It's using him. 😃

^^ THIS. 🥲

I'll definitely take you up on that offer @austinpe

I've been mostly enjoying Vue as I've been learning it (BrewFlasher Web, TronBridge) but have run into other projects that it's been giving me fits with (KegScreen's tap lists, Fermentrack's dashboard). If I had more time (and fewer projects) I've contemplated rewriting Fermentrack to be mostly REST + Vue rather than relying on Django templates, though I'll probably end up doing the same for KegScreen first.

austinpe, 2022-06-25:
Yeah, from my experience Django feels really 'heavy' vs just having the routing handled by Vue.
There are great, well tested libraries to handle REST within JS such as [Axios](https://github.com/axios/axios).

Obviously, we all use the tools we're most comfortable with and getting a project out and useable is the main goal.

My go to recently has been Vue3 + Tailwind; it has allowed me to build awesome projects very quickly and without being a designer.
I made two local brewery's websites with that combo: [King Maker Brewing](https://www.kingmakerbrewing.com/) and [Reve](https://www.revebrewing.com/)

But yeah, redoing Fermentrack to use Vue + Rest vs Django would possibly make it easier to maintain, but would be a ton of work.

lbussy, 2022-06-25:
Where I generally try to c-block John getting any attention, in this case him finishing KegScreen benefits me directly so I approve. 😛

lbussy, 2022-06-25:
Here ya go:  https://web.brewflasher.com/fw/78/

(in case it's broken again, it's under pre-releases Alpha.3.)

lbussy, 2022-06-26:
Any issues with this one @austinpe?

lbussy, 2022-06-26:
Well, I think it works now. :)  This was closed by #25 and merged into `devel`.

I'd like to get the TaplistIO work done and then release 1.1.0.

austinpe, 2022-06-26:
Good news and bad news again.

**Good news**
I confirm that the tap info report successfully sends now! 🥳

**Bad news**
I'm not sure what happened, but as of these last few builds I can no longer monitor serial out.
As soon as I connect via PuTTY it causes a panic (see log below).
Also, rebooting doesn't fix it. I have to hold the 'boot' button for a few seconds before it will properly reload the firmware.

If I don't connect on the serial line and just let it go then it works fine and I can interact with it via the webpage / API.

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

lbussy, 2022-06-26:
> I'm not sure what happened, but as of these last few builds I can no longer monitor serial out.

Opened #26 for this.

I monitor it via Serial, so it's very curious why you cannot.

Closed 2022-06-26.

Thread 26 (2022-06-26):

Controller Crash

lbussy, 2022-06-26:
From #20

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

```
    rst:0x1 (POWERON_RESET),boot:0x13 (SPI_FAST_FLASH_BOOT)
    configsip: 0, SPIWP:0xee
    clk_drv:0x00,q_drv:0x00,d_drv:0x00,cs0_drv:0x00,hd_drv:0x00,wp_drv:0x00
    mode:DIO, clock div:2
    load:0x3fff0018,len:4
    load:0x3fff001c,len:1044
    load:0x40078000,len:10044
    load:0x40080400,len:5872
    entry 0x400806ac

    1970-01-01T00:00:00Z N: Serial logging started at 115200.
    1970-01-01T00:00:00Z V: Starting WiFi.
    *WM: [1] Free heap: 246792
    *WM: [1] ESP SDK version: v3.3.5-1-g85c43024c
    *WM: [3] allocating params bytes: 20
    *WM: [2] Added Parameter: name
    *WM: [1] AutoConnect.
    *WM: [2] esp_wifi_set_country: US
    *WM: [2] ESP32 event handler enabled.
    *WM: [2] Connecting as WiFi client.
    *WM: [3] STA static IP:
    *WM: [2] setSTAConfig static ip not set, skipping.
    *WM: [1] Connecting to saved AP: REDACTED
    *WM: [3] Using password: REDACTED
    *WM: [3] WiFi_enableSTA: enabled.
    *WM: [3] Mode after delay: STA
    *WM: [2] 30000 ms connectTimeout set.
    *WM: ▒▒] 30000 ms timeout, waiting for connection................Guru Meditation Error: Core panic'ed (Interrupt wdt timeout on CPU0)
    Core 0 register dump:
    PC 0x40086e6 PS 0x00060834 A0 0x8012c10 A1 0x3fa3e
    A2 0x3fc604 A3 0x00000000 A4 0x00000000 A5 0x3fcd0
    A6 0x00000002 A7 0x00000100 A8 0x8008a44 A9 0x3fa3f
    A10 0x00000005 A11 0x00060c3 A12 0x00060c0 A13 0x3fa488
    A14 0x00000017 A15 0x00000000 SAR 0x00000020 EXCCAUSE 0x00000005
    EXCVADDR 0x00000000 LBEG 0x4000ce LEND 0x4000cf LCOUNT 0xffff

    ELF file SHA256: 000000000000000

    Backtrace:0x40086e6:0x3fa3e 0x4012c0d0x3fa420 0x4012c19:0x3fa450 0x40130ff0x3fa480 0x40089be0x3fa4b

    ore 1 register dump:
    PC 0x4018762a PS 0x00060834 A0 0x8016d1e A1 0x3fb7a
    A2 0x00000000 A3 0x00000001 A4 0x80089d0 A5 0x3fba0
    A6 0x00000000 A7 0x3fb4a A8 0x00060023 A9 0x3fb310
    A10 0x00000000 A11 0x00000001 A12 0x80089d0 A13 0x3fb8b
    A14 0x00000000 A15 0x3fb4a SAR 0x00000000 EXCCAUSE 0x00000005
    EXCVADDR 0x00000000 LBEG 0x00000000 LEND 0x00000000 LCOUNT 0x00000000

    ELF file SHA256: 000000000000000

    Backtrace:0x4018762a0x3fb7a 0x4016d1b0x3fb7c 0x4008b7d0x3fb7e 0x40089be0x3fb800

    Rebooting...
```

austinpe, 2022-06-26:
Hmm. The panic isn't just on Serial connection either.

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

I just checked the web interface and it seems the temp is slowly going up and up because the esp32 keeps rebooting due to a panic.
Then the thermostat never triggers because it's in "minimum off time" (which is fine). But, basically it seems that the device is not staying on for longer than 5 min at a time

lbussy, 2022-06-26:
Well that's strange. I looked at mine and it's definitely reset.  It sounds like mine is running longer:

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

Yay, library issues!

austinpe, 2022-06-26:
Here's another log dump on a freshly flashed esp32 and after setting up the wifi.
You can see that it connects, starts up, and then fails.

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

lbussy, 2022-06-26:
When I get done cooking I'll re-compile 1.0.0 and see if the problem persists.  If it does, it will be an upstream change.

lbussy, 2022-06-27:
Okay, I ran all night on 1.0.0.  Back on the Alpha code now.

austinpe, 2022-06-27:
I'll try out this version after work!

I noticed that it does go for longer than 5 min; it has gotten up to an hour or so. But, I can't seem to zero in on what causes it.

It was risky, but I let it run over night. The temp was within 1° of target, so it _is_ able to cool, but it's restarting constantly.

Here's the a screenshot as I'm writing this message to show that it can go over 5min but is still happening.

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

austinpe, 2022-06-27:
It seems the firmware is not longer in your github?
The address that BrewFlasher looks for is 404.

I looked in the 'debug reset' branch and it seems that the compiled firmware in there is a few days old, so I'm not sure if they are correct, but I'll try them.

lbussy, 2022-06-27:
Thaaaaats weird.

Gimme a sec. :)

thorrak, 2022-06-27:
> Thaaaaats weird.
>
> Gimme a sec. :)

Wasn't me. (this time)

lbussy, 2022-06-28:
No, it was me.  _Apparently_ when I delete a tag, the release it was tied to breaks.  Go figure.

austinpe, 2022-06-28:
I had a really hard time finding the recommended D32 for this project (Lolin D32 v1.0.0).
I found other ones for cheaper on amazon and just had to do a breadboard to the PCB header.

Did you re-release the debug build on github?

lbussy, 2022-06-28:
I did:

[1.0.1-Debug.1](https://github.com/lbussy/keg-cop/releases/tag/1.0.1-Debug.1)

John broke BrewFlasher again so you will have to do it manually.  Pay attention to the partition table changes, they are [listed here](https://github.com/lbussy/keg-cop/blob/reboot_timers/4mb_inc_ota.csv).

lbussy, 2022-06-28:
Key (helpful) change:  The system will log uptime and reboot reasons in `uptime.csv`.  Go to the `/edit` page (un: admin, pw: p@ssword) and right click the file to download the csv:

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

lbussy, 2022-06-28:
John fixed BrewFlasher:

https://web.brewflasher.com/fw/78/

austinpe, 2022-06-28:
awesome. I was having trouble with the new offsets. I'll try brewflasher now

austinpe, 2022-06-28:
I got it connected to the network.
Web interface loaded fine.

Tried to connect via Serial and had the following.
It seems that on connect it reboots the device, then panics, then reboots, panics, and then hangs.
I'll keep digging.
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

lbussy, 2022-06-28:
> Core was running in ISR context:

Disconnect any of your flowmeters and see what happens.

austinpe, 2022-06-28:
That was a new esp32 with nothing connected.

But, I started to think when you said you had to find a new esp32.
I just flashed another brand ESP32 (this one only has 30 pins instead of 38) and it has been up for 20min with both web interface and serial connected...

So, I wonder if the issue was with an incompatibility with this specific board+ libraries?
It's weird that both boards of the same brand had the panic and now this new one doesn't.

I'll keep monitoring

lbussy, 2022-06-28:
That could be - it makes sense.  WiFi and BLE use some pins on some boards and not others.  This was written on Lolin D32 (regular, not pro) so that may guide you a bit.

For what its worth, I did not change anything having to do with pins.

lbussy, 2022-06-29:
Here's the pinout:  https://www.wemos.cc/en/latest/d32/d32_pro.html

austinpe, 2022-06-29:
I just reflashed v1 on the board that was panicing.
No issues so far -- I can connect to both web and serial at the same time.
It's been up for 10min now.

So, it has to be some combo of new libraries (?) and the board.

Here's the pinout of the board that panics on the new version:
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

And here's the pinout of the board that seems to be doing ok (so far) with the new version:
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

austinpe, 2022-06-29:
Hmm. I spoke too soon about this new board.

<html xmlns:v="urn:schemas-microsoft-com:vml"
xmlns:o="urn:schemas-microsoft-com:office:office"
xmlns:x="urn:schemas-microsoft-com:office:excel"
xmlns="http://www.w3.org/TR/REC-html40">

<head>

<meta name=ProgId content=Excel.Sheet>
<meta name=Generator content="Microsoft Excel 15">
<link id=Main-File rel=Main-File
href="file:///C:/Users/Austin/AppData/Local/Temp/msohtmlclip1/01/clip.htm">
<link rel=File-List
href="file:///C:/Users/Austin/AppData/Local/Temp/msohtmlclip1/01/clip_filelist.xml">
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
lbussy, 2022-06-29:
Here's where we need to get you running with PlatformIO and you can try a few things.  Are you able to clone the repo and get this branch to compile?  If so I can suggest a few things to rule in/out some of the pin sets to narrow it down.

lbussy, 2022-06-29:
Also:  I have deleted the debug download and replaced it with `1.1.0-Alpha.1` to reflect the semantic versioning of what will be a release.

[Keg Cop 1.1.0-Alpha.1](https://web.brewflasher.com/fw/81/)

austinpe, 2022-06-29:
I'll try to download and compile on my own now.
I'll let you know how it goes!

I'm currently at 10 hours of uptime which I think is the longest stretch.
I was curious if the panics were related to interactivity or if they were random.
My keezer obviously doesn't get a ton of use during morning/day time, but I do have nitro coffee on tap that's being tracked, so it did get some use early this morning and didn't crash.

Also, I have it sending data to a server via the Keg Screen feature.

I just wanted to write out my full use case in case it has any helpful hints.

thorrak, 2022-06-29:
When was the last time you updated the espressif32 package in platformio?

lbussy, 2022-06-29:
> When was the last time you updated the espressif32 package in platformio?

I just installed PIO on here so not too long ago.

lbussy, 2022-06-29:
Yeah ... I've got work to do because of the new platform packages.

lbussy, 2022-06-29:
Updated [Keg Cop Alpha](https://web.brewflasher.com/fw/81/) to 1.1.0-Alpha.2

You'll have to `git fetch --all` and `git checkout taplist_io` to get this branch.  It _might_ fix the crashes - check it.

austinpe, 2022-06-29:
It got SO much further this time, but still had an issue in the Onewire library file OneWire_direct_gpio.h

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

lbussy, 2022-06-29:
Click on the alien, drop down lolin_d32 under Project Tasks, General. "Clean all":

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

lbussy, 2022-06-29:
You should try the one I added to BrewFlasher as well.

austinpe, 2022-06-30:
I'm trying the new one from BrewFlasher.

I tried the 'clean all' task and it for some reason ended up with a 'permission denied' error. I tried to troubleshoot this and everything seemed to just blame antivirus. I tried disabling everything, but still got the same error.
I tried running in admin mode.
I forked the repo and tried that in admin mode -- always the same error.

But, it seemed to help regardless as it allowed the 'build' task to get further. Now, it's an issue with

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

austinpe, 2022-06-30:
I know you're not here to provide platformIO support. I'll try to figure it out myself; I just wanted to update you on where I'm at.

lbussy, 2022-06-30:
That happens - Windows is especially challenging with that.

You can try to manually delete the ./.pio/libdeps directory inside the project.  That's effectively the same thing.  The end result we are looking for is forcing the library dependencies to update.

In the case of that particular error, it's the fault of a forced dependency that is not even used in this project.  Let me try to clean that up.  I prefer letting the upstream authors manage their own code but sometimes they don't have the same focus.

lbussy, 2022-06-30:
Updated [Keg Cop Alpha](https://web.brewflasher.com/fw/81/) to 1.1.0-Alpha.3

`git pull` on the `taplist_io` branch to get the current changes.  You'll probably want to do that clean command (or delete the `./.pio/libdeps` directory) to be sure.

austinpe, 2022-06-30:
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

lbussy, 2022-06-30:
Excellent! Try the current version in Brewflasher though, there have been a lot of platform changes which may help your stability issues.

lbussy, 2022-06-30:
Watchdog Timer.  Means it locked up for whatever reason.

austinpe, 2022-07-01:
It seemed good for as long as it was up (we just had a power surge).
I can't seem to download the uptime.csv anymore, though. The page loads, but right-click -> download doesn't result in anything.
I was checking the "about" page occasionally and I believe it was already at 16 hours or so before this power surge.

Anyways, the platform update seems to have resolved the crashing.
I'm flashing Alpha.4 right now and will keep you updated.
Feel free to mark this issue as resolved; I can always re-open if problems crop up again 😄

lbussy, 2022-07-01:
Yeah unfortunately the new platform libraries broke the SPIFFS editor.  Now in theory I should not need it when I am done, but I use it a lot in development.  Not sure what's up with that.

Closed 2022-07-01.

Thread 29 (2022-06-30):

Telemetry data visualization via Grafana [was: Question about MQTT topic structure and JSON packet schema]

amotl, 2022-06-30:
Dear Lee,

it is fun to see what you are working on over here. It looks like an excellent project. Kudos!

May I humbly ask you a specific question, as I see you are using MQTT within your architecture. In the README, it says:

> Keg Cop will report pours to Raspberry Pints via MQTT or a web endpoint with a generic JSON packet.

Can you outline the typical JSON message(s) emitted by this appliance, and the corresponding MQTT topic structure? Is it some measurement values?

I am asking because I am thinking that [Kotori] may be a sweet complement for your system [^1]. It is easy to write adapters for individual device families, and if that would fit together in any way, I will be happy to provide a corresponding adapter for Keg Cop.

With kind regards,
Andreas.

[Kotori]: https://github.com/daq-tools/kotori
[^1]: Edit: For effortless telemetry data recording and visualization via Grafana.

amotl, 2022-06-30:
Hi again,

I see that I asked too quickly before dedicating some time to browse the API documentation [^1] and the documentation of the JSON models [^2]. Apologies.

[^3] and [^4] would be the payloads which describe the measurement values emitted by the system, right? I am now also seeing that the _Controller-Initiated Communication_ part of the API would probably be the right thing what I was looking for.

Specifically:
> The Target URL Report provides a holistic picture of the system to a custom/third-party endpoint. It is a timer-based POST; a change of state does not trigger it. As with all target system configurations within Keg Cop, it will post to HTTP only.
>
> -- https://docs.kegcop.com/en/latest/api/#url

I think this would be the right choice for integrating with Kotori, if that would make actual sense.

By chance, on the screenshots you provided on the _Operations and Configuration_ pages [^5], I haven't seen any about displaying graphs of measurement values over time. Maybe I am missing them. On the other hand, if such a feature is not implemented within Keg Cop yet, but you think it would be nice to have, then I will be happy to support.

With kind regards,
Andreas.

[^1]: https://docs.kegcop.com/en/latest/api/index.html
[^2]: https://github.com/lbussy/keg-cop/tree/main/jsonmodels
[^3]: https://github.com/lbussy/keg-cop/blob/main/jsonmodels/Temps%20JSON.md
[^4]: https://github.com/lbussy/keg-cop/blob/main/jsonmodels/Flow%20JSON.md
[^5]: https://docs.kegcop.com/en/latest/operations/

lbussy, 2022-06-30:
The intention was always that this would be part of an extensible system of systems.  @thorrak has been "going to finish" [KegScreen](http://www.kegscreen.com/) for a while now.  Maybe if I get enough people to help me shame him, he will. 😉

Anyway, so if such a picture over time were desired, the "upstream" should handle that.

My main target was to be the "physical" connection and own those measurements, where KEgScreen would build the fancy tap list.

amotl, 2022-07-01:
All right. Maybe @thorrak is interested as well, otherwise I will not step on anyones toes. I am looking at eyecandy like the weather dashboards we are operating over at https://weather.hiveeyes.org/, for example [^1].

It is sweet to determine long-term trends and get a different grip on the telemetry data which is already emitted by the system. As mentioned above, I don't even know if that would be an actual benefit to your community at all. Probably it would be a better fit for a brewing rig?

[^1]: https://weather.hiveeyes.org/grafana/d/YVm0P1miz/meteogramm-messwerte-and-vorhersage

lbussy, 2022-07-01:
You are absolutely not out of line, I'm all ears.  That's the best part of Open Source, everyone's ideas count.

I'll poke John to read this and see what he thinks.  It's possible there's complimentary work to what he wants to do.

lbussy, 2022-07-29:
Hey @amotl, I am going to close this as not an issue - but if you are interested in this project and you'd like to see additional support in MQTT, for instance, let me know.  Right now, I think the webhook functionality could send JSON anywhere you like and be ingested as JSON.  I had another question about a complete (and standards-based) MQTT setup, so it's rolling around in my head for use.

Closed 2022-07-29.

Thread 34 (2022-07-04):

SPIFFS Editor is broken

lbussy, 2022-07-04:
With the new libs and platform libs, SPIFFS Editor is broken (`/edit`.)  This will not be enabled when in `release` mode, however it's annoying as hell and I am going to leave this open till I fix it or get tired of seeing this issue open.

lbussy, 2022-08-04:
Pretty sure this is related to SPIFFS requiring a leading `/` in the filename:

`[ 47714][E][vfs_api.cpp:29] open(): {filename} does not start with /`

I have tried (briefly) to see if we can go to LittleFS but the filesystem image in LittleFS is too large for the current partition.

lbussy, 2022-09-01:
Supposedly [lorol's implementation](https://github.com/lorol/ESPAsyncWebServer) works.

The compare is [here](https://github.com/me-no-dev/ESPAsyncWebServer/compare/master...lorol:ESPAsyncWebServer:master).

Down and dirty attempt to use it failed due to partition size limitations.

lbussy, 2022-09-09:
Added a vestigial filesystem editor in `feature1.2`.

Closed 2022-09-09.

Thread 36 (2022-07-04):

Multiple names for sensor enabled/sensor calibration settings

thorrak, 2022-07-04:
Similar to #35, the various temp sensor settings are called different things depending on if it's in the JSON being emitted or the form being posted back. Example for the room sensor:

Called "calroom" / "enableroom" when being posted back: https://github.com/lbussy/keg-cop/blob/bde8c08835e458cf0ff198d6b74ee577ccd34d9d/src/webpagehandler.cpp#L815

but just called "room" / "roomenabled" when being emitted in the JSON: https://github.com/lbussy/keg-cop/blob/bde8c08835e458cf0ff198d6b74ee577ccd34d9d/src/jsonconfig.cpp#L449

lbussy, 2022-07-04:
Admit it - you hated seeing me close out all those other issues.

thorrak, 2022-07-04:
When you get bored, you start new projects. Just looking out for the rest of us here!

lbussy, 2022-07-04:
Fix in `devel`.

Closed 2022-07-04.

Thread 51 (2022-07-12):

Errors and then only 404 pages after clicking on main page Temp Bar or Control point: Keg Sensor link

rkhanso, 2022-07-12:
I've posted some info at https://www.homebrewtalk.com/threads/keg-cop-keg-monitoring-and-control.692880/page-6#post-9300514

When I click on the tan(ish) bar showing temperature on the main Keg Cop (ESP32) web page, I get two error messages:
Settings Error: Settings update failed.
Temps Warning: Unable to retrieve temperature data.

After that happens, when I use the menu to choose any other page, I get a 404 error. The only page that doesn't happen on is the external Keg Cop documentation menu link.  I can't get out of the 404 error loop using the menu at all. Only when I manually remove the /404 in the URL can I get back to the Keg Cop (ESP32) web gui.  This also happens when I'm on the Temperature Sensors for Kegerator page and click on the link "Control point: Keg Sensor"  -- the same exact results as previously explained.

If I never click on those two links, the Keg Cop web page (ESP32) works perfectly.

I get the same results in both Brave and Edge browsers.

lbussy, 2022-07-12:
I don't have temperature sensors hooked up at the moment (insert long story/standard disclaimer about me moving), so I need to get that set up before I can do any testing.  I have if/then blocks in C++ and JS to take different paths if there are no temp sensors detected.

rkhanso, 2022-07-12:
Your comment made me think about my configuration. I have space in the single-sided PCB for 3 temp sensors, but only have one connected at the moment. I checked my Keg Cop config and see that I had 2 other sensors enabled. Thinking this might be the cause of the error and the 404 loop, I disabled all but the one sensor actually connected at this moment....but it didn't make any difference. Still the same error messages as well as the 404 loop after clicking on those two links mentioned above.

lbussy, 2022-07-12:
Yeah either way it should not `404` so I broke something.  :)

lbussy, 2022-07-17:
Took care of the 404 loop under #60, which was a separate issue.  Looking at the reason the temps page is broken now.

rkhanso, 2022-07-26:
Hello Lee,

I’ll give the Development release a try. I still notice that the 404 error loop is there in the main 1.1.0 version.

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

lbussy, 2022-07-26:
Give me about an hour to push a new `devel` version.  I think I have it licked.

lbussy, 2022-07-26:
Okay - `devel` should be good to test.

rkhanso, 2022-07-26:
I also noticed a spelling error – Temperatire

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

rkhanso, 2022-07-26:
I just noticed an inconsistency in the Taps Settings/Configuration.

In the dropdown for Taps, it shows 1-9

When you choose a tap, it shows in the GUI the correct tap number for all except for Tap 9 (It says Tap 8 Configuration)

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

lbussy, 2022-07-26:
> When you choose a tap, it shows in the GUI the correct tap number for all except for Tap 9 (It says Tap 8 Configuration)

Man if that's all you've found I did pretty good!  :)

Got it, fixed in my local version and will be in the release.

lbussy, 2022-07-26:
Okay - your email responses are getting messy and I am missing things.  Can you trim the old responses when you reply?

> I also noticed a spelling error – Temperatire

Added #68

> When you choose a tap, it shows in the GUI the correct tap number for all except for Tap 9 (It says Tap 8 Configuration)

Added #69

> When looking at the “Temperatures” page and clicking on one of the tan/orange temperatures shown, it goes to a bad link (see in the screenshot below)

No images come through when you reply via email.  You either need to click on the "View in GitHub" or describe more thoroughly.  Right now I am unable to reproduce this one.

> I can’t calibrate the flow meter with the new devel firmware. I was able to successfully calibrate it in 1.0.0, however.
>
>When I go to the calibrate page, Select Tap 9 (that’s the one and only I’m using since the 1-sided PCB made it easier), Config by volume, enter in some ounces measured, but don’t get a 0 to show up in the Pulses box until the flow starts. No pulses seen at all.

Not following here either.  You should not enter ounces until after you have dispensed the volume, then enter ounces, then it should calibrate.  Is that not working like that?

rkhanso, 2022-07-26:
Regarding calibrating trouble:

When calibrating the flow meter I choose the correct tap (#9) and then check the Volume button and press “Do Config by Volume".

In the older versions of firmware, on the next screen a 0 would populate right away in the Pulses box and when I got some flow going, the count would increase.

In the Development firmware, a zero doesn’t immediately show up in the Pulses box and nothing happens when get some flow going. Pulses don’t increment, but the fact that it behaves different between v1.0.0 and devel makes me think it’s a firmware/coding problem and nothing on my end. It doesn’t matter whether I enter any ounces first or not, it doesn’t appear to count pulses. I’ve tried choosing different Tap numbers and that doesn’t make any difference either (didn’t expect it to though).

If I go back to V 1.0.0, I can calibrate with no trouble.

I put a screenshot on the homebrewtalk thread.

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

lbussy, 2022-07-27:
> When calibrating the flow meter I choose the correct tap (#9) and then check the Volume button and press “Do Config by Volume". In the older versions of firmware, on the next screen a 0 would populate right away in the Pulses box and when I got some flow going, the count would increase. In the Development firmware, a zero doesn’t immediately show up in the Pulses box and nothing happens when get some flow going. Pulses don’t increment, but the fact that it behaves different between v1.0.0 and devel makes me think it’s a firmware/coding problem and nothing on my end. It doesn’t matter whether I enter any ounces first or not, it doesn’t appear to count pulses. I’ve tried choosing different Tap numbers and that doesn’t make any difference either (didn’t expect it to though).

I've opened #70 for this.

Be sure to follow the new issues for these, as this one was for the 404 and is closed.

lbussy, 2022-07-29:
Updated [Keg Cop Beta](https://web.brewflasher.com/fw/90/) to 1.1.1-Beta.2

rkhanso, 2022-10-11:
Thanks,

The 404 problem certainly appears to be fixed. But I do now get a different problem. It looks like a possible typo in the web page link.
When looking at the “Temperatures” page and clicking on one of the tan/orange temperatures shown, it goes to a bad link (see in the screenshot below)

192.168.2.247settings.htm’s DNS address could not be found. Diagnosing the problem.

DNS_PROBE_POSSIBLE

Another thing that I think is wrong in the new code, but I can’t be 100% positive since my wiring or homemade PCB may be suspect…..

I can’t calibrate the flow meter with the new devel firmware. I was able to successfully calibrate it in 1.0.0, however.

When I go to the calibrate page, Select Tap 9 (that’s the one and only I’m using since the 1-sided PCB made it easier), Config by volume, enter in some ounces measured, but don’t get a 0 to show up in the Pulses box until the flow starts. No pulses seen at all.

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

lbussy, 2022-10-11:
Moved these to #149 and #150.

Closed 2022-07-20.

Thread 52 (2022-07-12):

Documentation Error

lbussy, 2022-07-12:
The page `docs/planning/index.rst` has an error:

> Daisy-Chain Boards: These small boards, one per flowmeter, connect the flowmeter(2) into the system. There is an “In” and an “Out” port, creating a chain of up to six sensors. The first on the chain is always number one, and so on.

This is a throwback to an earlier design and should show a max of nine sensors in a 3-3-3 configuration.

lbussy, 2022-07-29:
Updated [Keg Cop Beta](https://web.brewflasher.com/fw/90/) to 1.1.1-Beta.2

Closed 2022-07-17.

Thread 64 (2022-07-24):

Settings Error: Settings update failed.

ceesnz, 2022-07-24:
Version 1.0.0 works fine
Just installed version 1.1.0. Reconnected to my wifi.  that works. Web page works. However, none of the settings changes can be saved. Getting error Settings Error: Settings update failed.
Not sure where and how to debug

lbussy, 2022-07-24:
Yep, working on this.  Need a couple more hours of peace to knock it out.  Hopefully tomorrow.

ceesnz, 2022-07-24:
Thanks,
Just stumbled across your project today.  Looks awesome.
I went down the Kegbot/kegboard rabbit hole first and that project, even though impressive, is far too complicated.
Yours looks great. Can’t wait to see what KegScreen integration is going to look like.

Don’t have your pcb’s yet but will very likely get them.
I found the pins you use so manage to test without pcb

If your not to busy can you tell me if your project updates to a mqtt server and how often.  I might be able to integrate this into my Home Assistant project

Cheers for New Zealand

Cees
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

lbussy, 2022-07-25:
> Can’t wait to see what KegScreen integration is going to look like.

Me too.  I keep bugging @thorrak about it. :)

> If your not to busy can you tell me if your project updates to a mqtt server and how often.  I might be able to integrate this into my Home Assistant project

Right now MQTT is rather (okay, VERY) basic.  I put it in so that people who are emotionally invested in Raspberry Pints could use these controllers.  You can check the [API](https://docs.kegcop.com/en/latest/api/index.html) page and see the [RPints MQTT format](https://docs.kegcop.com/en/latest/api/index.html#raspberry-pints).  It's not "real" MQTT, but it does report each pour.

I'm not against adding more complete reporting via MQTT, I've just not had anyone want to use it yet.

lbussy, 2022-07-26:
Updated [Keg Cop Beta](https://web.brewflasher.com/fw/90/) to 1.1.1-Beta.1

lbussy, 2022-07-26:
I just pushed changes to `devel` in which this is fixed.

austinpe, 2022-07-27:
It might be my esp32, but with 1.1.1-Beta.1 an AP doesn't initiate upon successful FLASH.
Further, trying the double reset and grounding pin 13 didn't raise the AP either.

I didn't have a lot of time; I'll try tomorrow with another esp32.

lbussy, 2022-07-27:
> It might be my esp32, but with 1.1.1-Beta.1 an AP doesn't initiate upon successful FLASH.

I'd recommend watching the serial monitor and seeing what's going on there.  That may be the most highly tested area of the whole thing. :)

If I reset, wait about half a second and then reset again (the feature times out after 3 seconds), I get this:

```
1970-01-01T00:00:00Z N: Serial logging started at 115200.
1970-01-01T00:00:00Z N: DRD: Portal requested.
1970-01-01T00:00:02Z N: Entered portal mode; name: kegcop, IP: 192.168.4.1.
```

austinpe, 2022-07-27:
😄 it was my USB cable. Not enough voltage caused brown out trigger.
My mistake!

lbussy, 2022-07-29:
Updated [Keg Cop Beta](https://web.brewflasher.com/fw/90/) to 1.1.1-Beta.2

Closed 2022-07-27.

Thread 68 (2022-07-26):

Spelling Error in Settings

lbussy, 2022-07-26:
> I also noticed a spelling error – Temperatire

lbussy, 2022-07-27:
Fixed in 'devel'.

lbussy, 2022-07-29:
Updated [Keg Cop Beta](https://web.brewflasher.com/fw/90/) to 1.1.1-Beta.2

Closed 2022-07-27.

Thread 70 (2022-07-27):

Flowmeter calibration Issue

lbussy, 2022-07-27:
> When calibrating the flow meter I choose the correct tap (#9) and then check the Volume button and press “Do Config by Volume". In the older versions of firmware, on the next screen a 0 would populate right away in the Pulses box and when I got some flow going, the count would increase. In the Development firmware, a zero doesn’t immediately show up in the Pulses box and nothing happens when get some flow going. Pulses don’t increment, but the fact that it behaves different between v1.0.0 and devel makes me think it’s a firmware/coding problem and nothing on my end. It doesn’t matter whether I enter any ounces first or not, it doesn’t appear to count pulses. I’ve tried choosing different Tap numbers and that doesn’t make any difference either (didn’t expect it to though).

lbussy, 2022-07-29:
Working on this one now.

lbussy, 2022-07-29:
I added myself the ability to add pulses manually (by typing) so that I can debug this one.  A lot of work for that, but I don;t have any flowmeters at hand.

lbussy, 2022-08-03:
Closed (finally!) and in `devel`.  Beta release pending.

lbussy, 2022-08-03:
Updated [Keg Cop Beta](https://web.brewflasher.com/fw/90/) to 1.1.1-Beta.3

Closed 2022-08-03.

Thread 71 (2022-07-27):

Temp sensor calibration doesn't seem to work in v1.1.1-Beta.1 [devel] (817678a)

rkhanso, 2022-07-27:
Similar to a previous and now closed issue #9, when I change the numbers on the Temperature Sensor Control page, nothing changes in the temperature output on the Temperature Sensors data page. Calibration is not possible.

lbussy, 2022-07-29:
This is fixed in `devel` (not available in BrewFlasher Beta yet.)

lbussy, 2022-07-29:
Updated [Keg Cop Beta](https://web.brewflasher.com/fw/90/) to 1.1.1-Beta.2

Closed 2022-07-29.

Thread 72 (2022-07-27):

Malformed links when using IP instead of mDNS

rkhanso, 2022-07-27:
When on the Temperatures page and clicking on any of the tan/orange temperature graph/columns, the link it wants to take you doesn't exist.  It appears to want to take you to the Settings page, but the URL has a typo.

http://192.168.2.247settings.htm/#sensorcontrol   <<<---where it wants to take me, but a bad link.
http://192.168.2.247/settings/#sensorcontrol  <<<--- I think this is where you intended it should take me.

lbussy, 2022-07-27:
"You people" that don't use mDNS ... :)

Do you have the ability to test by name?  More at:

https://docs.kegcop.com/en/latest/troubleshooting/index.html

rkhanso, 2022-07-27:
I installed the Bonjour Browser and only get spinning circle. Nothing ever populates in the "Available Bonjour Services" window.

I checked my Windows security settings. I have the LAN firewall (Domain Network and Private Network) turned off.  If there are other security settings that might need to be adjusted, I'm not sure what they'd be. I also have an Untangle Firewall, but since this should be scanning Local traffic, I'm not sure that would actually come into play (though I do have 3 VLANs). Everything else on the LAN works OK. No trouble.

rkhanso, 2022-07-27:
I'm sorry to have brought this issue up now. I did get MDNS sort of working and am able to access the ESP32 via //kegcop/ now and the web pages work correctly.

But I'm sure I won't be the last person using the IP address instead of hostname in the URL.

lbussy, 2022-07-27:
Ah just teasing you.  I need to get it fixed because there are some folks who for whatever reason cannot use mDNS.

lbussy, 2022-07-27:
This is fixed in `devel`.

rkhanso, 2022-07-27:
Is the devel you mention below different than the version that Brewflasher will use? I ask, because I used Brewflasher to get the devel firmware and it’s still looking like a bad link when using the IP address for URL.

Or might I need to wait until a new devel version is uploaded to Brewflasher or download the newest update somewhere else?

I need to go back to version 1.0.0 anyway, because that’s the only version that the flow meter works for me.

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

lbussy, 2022-07-27:
> Is the devel you mention below different than the version that Brewflasher will use?

Yes.  When I get one or two more things fixed I'll post another to BrewFlasher.

lbussy, 2022-07-29:
Updated [Keg Cop Beta](https://web.brewflasher.com/fw/90/) to 1.1.1-Beta.2

Closed 2022-07-27.

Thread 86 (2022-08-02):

Feature request - convert the Solenoid pin to a Temperature Controlled option for a Tower Fan

rkhanso, 2022-08-02:
I have a tower temp probe and a fan to blow cold air up there when needed. The fan is pretty noisy and I don't want it running all the time.
I currently use CraftbeerPi3 to control my Kegerator and it has the ability to turn the fan on/off based on the tower temperature probe. Could you add this feature into KegCop so that it can do the same?

lbussy, 2022-08-02:
This should be possible to do by swapping the solenoid pin over to be used by a thermostat control.  Putting it in the "enhancements" list.

lbussy, 2022-08-08:
Something like this?

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

rkhanso, 2022-08-09:
Perfect!

lbussy, 2022-08-09:
Right, I think I have like a 10 second min time to keep it from hammering the relay should something go wrong.

I need to test it and all that, but the bones should be there anyway.

lbussy, 2022-08-12:
If you want to test this, BrewFlasher has been updated to [Keg Cop Alpha](https://web.brewflasher.com/fw/90/) to 1.2.0-Alpha.1.

This should be the release I made earlier tonight (1.1.1) with all the bug fixes plus the Tower Fan.

I am headed out for a week and a half, so if you have issues just note them here and I'll get them when I get back.

lbussy, 2022-08-24:
Okay this is in `feature1.2` now.  @thorrak will be adding a "try this" for you here in a few (to see if your SPIFFS memory is bad) and you can test this code.  Under -> Settings -> Temperature -> Control, you can enable the Tower Fan control and setpoint.  When this is enabled, the "Solenoid" control will be disabled as this repurposes that pin.

Here's the control section:

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

This is how the icon looks when not on:

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

This is how it looks when it is on/blowing:

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

I'm closing this now as "complete."  It will be in 1.2 when I release it.

Closed 2022-08-24.

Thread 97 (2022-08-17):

Crash during page loads

lbussy, 2022-08-17:
As reported in [this post](https://www.homebrewtalk.com/threads/keg-cop-keg-monitoring-and-control.692880/page-7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) there may be an issue with the number of connections or how they are stored.  When using @thorrak's branch, so far, the crashes seem diminished/eliminated.  Tracking an [issue here](https://github.com/lbussy/AsyncTCP/issues/2).

lbussy, 2022-08-20:
Pretty sure we got to where @thorrak just recompiled the same base code, and it worked.

lbussy, 2022-09-09:
This is addressed with local user items as well as enhancements to the UI.

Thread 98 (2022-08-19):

mDNS service discovery (dns-sd) doesn't reliably work

thorrak, 2022-08-19:
Unfortunately, mDNS service discovery doesn't seem to reliably announce the `_kegcop._tcp.` service when attempting to browse services on the network.

I think this relates to https://github.com/espressif/arduino-esp32/issues/7156

lbussy, 2022-08-19:
That's an interesting one.

thorrak, 2022-08-19:
With that PR it works perfectly, without it, no dice. Go figure. :(

lbussy, 2022-08-20:
Merged into `devel`.

Closed 2022-08-20.

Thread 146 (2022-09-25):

404 on Temp Bar

lbussy, 2022-09-25:
Somehow in all the fun I re-introduced a 404 issue when clicking on a temperature bar on `/temps/`.

lbussy, 2022-09-25:
Fixed in `devel` ... again.

Closed 2022-09-25.

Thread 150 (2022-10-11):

Calibration Error

lbussy, 2022-10-11:
I can’t calibrate the flow meter with the new devel firmware. I was able to successfully calibrate it in 1.0.0, however.

When I go to the calibrate page, Select Tap 9 (that’s the one and only I’m using since the 1-sided PCB made it easier), Config by volume, enter in some ounces measured, but don’t get a 0 to show up in the Pulses box until the flow starts. No pulses seen at all.

_Originally posted by @rkhanso in https://github.com/lbussy/keg-cop/issues/51#issuecomment-1274170349_

lbussy, 2022-10-12:
> don’t get a 0 to show up in the Pulses box until the flow starts. No pulses seen at all.

@rkhanso I want to be sure I understand this.  Why would it matter if the 0 shows up or not if you have not started flow?  The process for "By Volume" is:

1. Select "by volume"
2. Draw a sample of a known volume (e.g. 12 ounces)
3. (at this point pulses should register)
4. Enter "12" as the volume dispensed
5. The calculated PPU should be displayed

7. Enter "12" in the

rkhanso, 2022-10-13:
Keg Cop quit working for me again. I think I'm going to have to go back to use CraftbeerPi3 for now on the Kegerator. I may try Bru Control in the future for all aspects of my brewing process.

From my memory though...
the 0 didn't pre-populate in the pulses box after I chose to calibrate, which then made it impossible to calibrate the flow meter. I knew this right away, because when there was a 0 in that box, I could change the number in the box. No zero in the box, the calibration number could not be entered and calibration was not possible.

lbussy, 2022-10-13:
> Keg Cop quit working for me again.

In what way?  Mine has been running (without actually pulling beer) for two weeks or so.  I need to ficx the me not getting any beer part.

> From my memory though...

I'll have to try to set some time aside to work through that.  I'm still not sure if it's a documentation problem or a code problem.  Either way it's my problem I'm just not sure which.

rkhanso, 2022-10-13:
It's been hit or miss whether I can get the web pages to load. It still seems to be rebooting randomly and losing configs. I have to go back in and reset the sensors, brewery name, etc.

Wouldn't you know.....right now it seems to be working.

Eventually it'll stop and the kegerator won't be told to turn on and it'll be 68F in it again.

rkhanso, 2022-10-13:
But now it just went berzerk again.  I clicked to go to the settings page and everything was reset - the 3 temp probes went to disabled. Control was then lost since there are no temps to control.

The only thing that doesn't get reset is the Tap settings. They stick. Everything else is lost when "it" happens

rkhanso, 2022-10-13:
One thing that I think would be helpful - some feedback after clicking the Update button on the settings page. I get no response that it accepted my changes. It just stays on that page and it looks like nothing happened until I leave it and go back (if it doesn't then reset itself again).

lbussy, 2022-10-13:
> One thing that I think would be helpful - some feedback after clicking the Update button on the settings page. I get no response that it accepted my changes. It just stays on that page and it looks like nothing happened until I leave it and go back (if it doesn't then reset itself again).

There is - the button will disable and show a spinning icon while it is applied.  If it goes back to normal then it is applied.  If not, there will be an error banner.

rkhanso, 2022-10-15:
I don't get a spinning circle. I get nothing confirming or denying the changes were saved or not.

I still keep getting the sensors and control resetting very frequently. Sometimes within 20 seconds after setting them up. The Tap settings are still there, but the temp sensors all go disabled and the temp control is disabled.

I'm going to stick with CraftbeerPi3 on the Kegerator.

rkhanso, 2022-10-29:
Is there a big difference in v 1.1.1 and 1.2.0-alpha?

The 1.1.1 version runs way better for me than the 1.2.0 version.

1.2 is very slow between web pages or doesn’t load them at all. The ESP crashes.

1.1 is very stable and fast.

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

lbussy, 2022-10-29:
> Is there a big difference in v 1.1.1 and 1.2.0-alpha?

Well, 1.2.0-Alpha is no longer supported; I released 1.2.0 officially, so if you are going to use a version, you should use that.

There are several changes between them, but the largest change is the core libraries from the manufacturer.  They are considerably larger and, by all accounts, do bring some additional quirks.

rkhanso, 2022-10-29:
Are there big differences in the web server, web pages, file system or basic underlying systems?

I ask, because I can run v 1.1.1 perfectly with fast web page response, no trouble loading pages for weeks so far.

But when on any of the 1.2 versions, the only web page that almost always opens is the home or about page. Often the temperature page doesn’t even show up in the menu and the setup page almost never loads (gets spinning circle). It still crashes frequently and I lose temp sensor settings, sometimes within a minute of setting them.

The reason I wanted v1.2 was to get the tower temp sensor to control the solenoid GPIO for a tower fan. I’ll gladly forget about that feature and just run 1.1.1 if that’s what it takes for the whole thing to be stable.

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

lbussy, 2023-04-13:
Fix merged to devel, closing.

Closed 2023-04-13.

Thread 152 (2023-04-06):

Fail to Update with Extended Volume Precision

lbussy, 2023-04-06:
From Danb35 on HBT:

> I started moving all the information down--tap 4's name/volume to tap 5, tap 3 to tap 4, etc. But when I went to put tap 1's information into tap 2, tap 2 started behaving the same way--no response at all to the update button. Turns out the remaining volume (which I'd copied from Raspberry Pints) had too many digits (3.32419). Shortening it to 3.3242 allowed it to accept the value. So then I moved all the data back up one slot, and tap 1 saves properly now. There's surely no need to measure volume to 0.00001 gal., but this seems an odd failure mode.

lbussy, 2023-04-12:
This is because the HTML `step`attribute is [set to .0001](https://github.com/lbussy/keg-cop/blob/18b27a26f8069bee98eceab7c63890783f225092/data/settings.htm#L230-L231).  I can always add zeroes, but that feels like a dumb idea.

lbussy, 2023-04-12:
Well ... that was easy.  Merged to `devel` and tested.

Closed 2023-04-12.

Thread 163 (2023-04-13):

Crash when debugging flow

lbussy, 2023-04-13:
The subroutine that allows manually entering pours seems to be generating watchdog resets when using the web interface as well

For anyone else reading this, this is NOT a user workflow bug, this is just something that bugs me.

lbussy, 2023-04-21:
This one is more complex.  It was while entering tap commands and pulling some other stuff like flow data for a web page (should be an extreme edge case.)  Pushing this one for now.

Closed 2023-04-23.

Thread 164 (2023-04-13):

WiFi Disconnect and Failed Reconnect

lbussy, 2023-04-13:
On occasion, the WiFi connection will disconnect and fail to reconnect:

```
[WiFi-event] event: 5
2023-04-12T14:17:46Z W: WiFi lost connection, reconnecting ..
[WiFi-event] event: 5
[WiFi-event] event: 4
[WiFi-event] event: 7
[WiFi-event] event: 1
[WiFi-event] event: 5
[WiFi-event] event: 4
[WiFi-event] event: 7
[WiFi-event] event: 1
[WiFi-event] event: 5
[WiFi-event] event: 4
[WiFi-event] event: 7
2023-04-12T14:18:03Z N: Reboot request - rebooting system.
[WiFi-event] event: 5
[WiFi-event] event: 3
```

This seems to be the same as [Wifi connection fails - only works after router reboot #8412](https://github.com/esp8266/Arduino/issues/8412) in the ESP8266 core for Arduino, and is explained REALLY well in [ESP32 STA deauth frame causing reconnect issues (IDFGH-6544) #8192](https://github.com/espressif/esp-idf/issues/8192).  The tracing tablatronix did here almost mirrors what I saw.

So now, I get to find a more graceful way (e.g. a hack) to recover from this because even if the newer core is better, it exhibits quite a bit more instability.

Thankfully, this results in a controlled restart (under Keg cop control) so it's not horrible.  The worst part of it is that the compressor lockout may cause a kegerator to be off while that timeout runs out.

thorrak, 2023-04-13:
Did you actually fire up wireshark and see the same deauth frame coming through? I ask, as that's something I was experiencing personally earlier, but have not been experiencing since more recent versions of esp-idf (via more recent Arduino framework releases) have been available

lbussy, 2023-04-16:
"Good enough" for now.  There is a compile-time define for `TRY_WIFI_RECONNECT` in `wifihandler.cpp` if I want to try again.  Right now it reboots on WiFi failure.

Closed 2023-04-16.

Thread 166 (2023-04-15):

Temp Sensor and Control Settings Wiped

lbussy, 2023-04-15:
On some resets (such as when a new firmware is pushed) the temperature sensor and control settings get cleared.

lbussy, 2023-04-21:
Fixed with #174

Closed 2023-04-21.

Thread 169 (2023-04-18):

Settings Loss on Power Cycle

lbussy, 2023-04-18:
> Theme, brewery name, kegerator name, temp sensors, and at least the Raspberry Pints target reset on power cycle. Tap information doesn't. There's still zero action on MQTT on a pour; log in the next post.
> Unplugging the USB cable used to flash the new firmware and check the logs, and plugging in the USB charger.

lbussy, 2023-04-21:
Fixed with #174

Closed 2023-04-21.

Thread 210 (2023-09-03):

Dropdown Arrow Missing In Calibrate Section for Taps

MichaelPersico, 2023-09-03:
When selecting a tap from the Calibrate section, the arrow for the dropdown is missing.  This makes you hold the left mouse button in order for the menu to appear.  Could not get menu the working at all on a tablet

lbussy, 2023-09-03:
What browser?

MichaelPersico, 2023-09-03:
> What browser?

Chrome on both computer and tablet.

lbussy, 2023-09-29:
I have not forgotten you - just swamped at work and home right now.

lbussy, 2024-02-20:
I'll bet you thought I forgot. ;)

Here's a direct link.  Please be aware that I do not have a board to test with, although _it should work_™.

[Keg Cop 1.3.1-Beta.1](https://web.brewflasher.com/fw/176)

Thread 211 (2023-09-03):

Clicking Renumbered Taps From Main Screen Takes You To Wrong Tap Settings

MichaelPersico, 2023-09-03:
When clicking a tap on the main screen it seems to only follow a numerical order no matter what taps are inactive or renumbered.  I currently have taps 1, 2, 4, and 5 active.  I have also renumbered taps 4 and 5 to show up as 3 and 4 on the home screen.  When clicking the renumbered tap 3, which is actually tap 4, it takes me to tap 3 settings even though tap 3 is inactive.

lbussy, 2023-09-03:
Unfortunately, this is a data versus display thing.  Each tap has a discrete pin, so they stay that way internally.  I allowed a "label" to renumber it, but you will always be skipping slots.  If @thorrak ever writes the elusive KegScreen, it will remove this hardware correlation.

lbussy, 2023-09-29:
Closing this one as "working as designed."  If a new idea pops up to address this hardware vs. UI issue, I'm all ears.

Closed 2023-09-29.

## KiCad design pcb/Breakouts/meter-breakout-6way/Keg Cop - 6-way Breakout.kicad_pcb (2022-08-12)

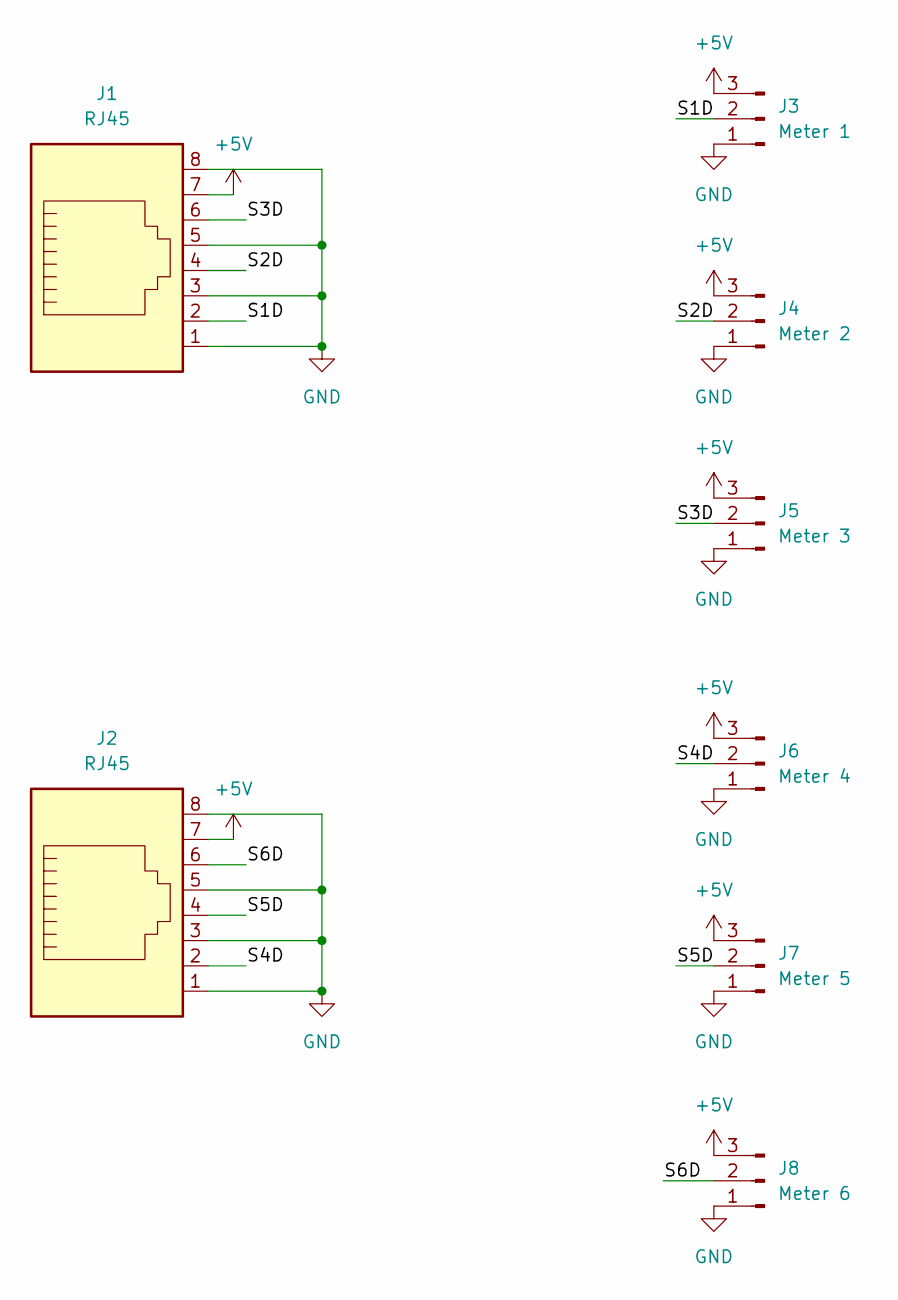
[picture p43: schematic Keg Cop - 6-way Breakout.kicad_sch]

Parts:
J1, J2: RJ45; RJ45_Amphenol_54602-x08_Horizontal
J3: Meter 1; JST_XH_B3B-XH-A_1x03_P2.50mm_Vertical
J4: Meter 2; JST_XH_B3B-XH-A_1x03_P2.50mm_Vertical
J5: Meter 3; JST_XH_B3B-XH-A_1x03_P2.50mm_Vertical
J6: Meter 4; JST_XH_B3B-XH-A_1x03_P2.50mm_Vertical
J7: Meter 5; JST_XH_B3B-XH-A_1x03_P2.50mm_Vertical
J8: Meter 6; JST_XH_B3B-XH-A_1x03_P2.50mm_Vertical

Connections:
+5V: J1.7, J2.7, J3.3, J4.3, J5.3, J6.3, J7.3, J8.3
/S1D: J1.2, J3.2
/S2D: J1.4, J4.2
/S3D: J1.6, J5.2
/S4D: J2.2, J6.2
/S5D: J2.4, J7.2
/S6D: J2.6, J8.2
GND: J1.1, J1.3, J1.5, J1.8, J2.1, J2.3, J2.5, J2.8, J3.1, J4.1, J5.1, J6.1, J7.1, J8.1

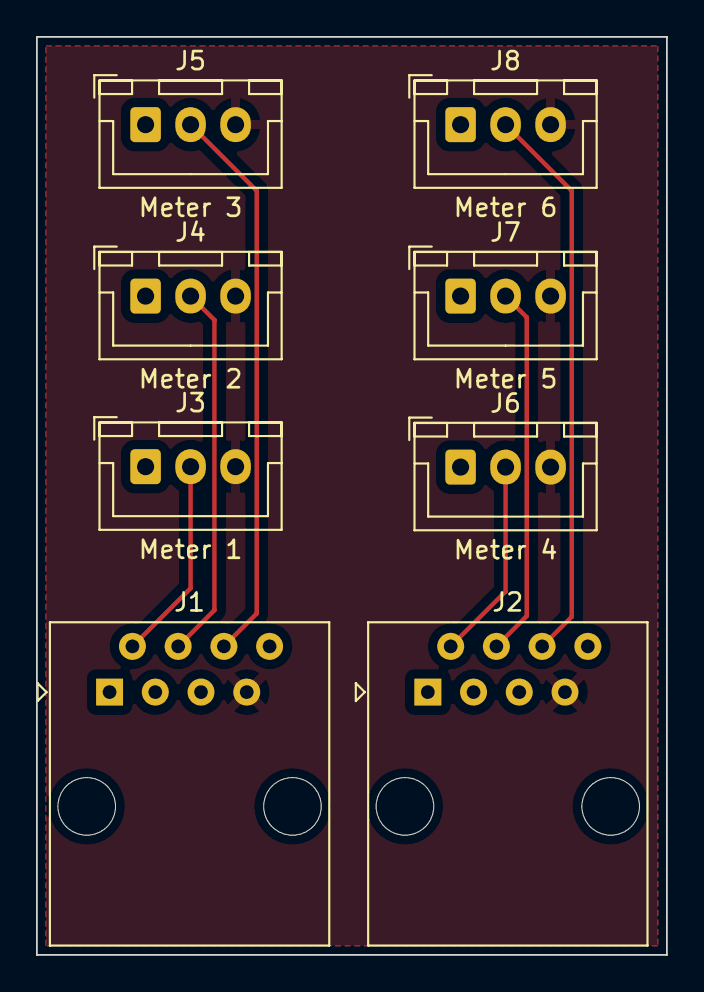
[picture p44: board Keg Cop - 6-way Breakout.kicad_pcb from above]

Board: 2 copper layers, 35.0 x 51.0 mm, 8 parts (0 on the bottom side), 8 nets.

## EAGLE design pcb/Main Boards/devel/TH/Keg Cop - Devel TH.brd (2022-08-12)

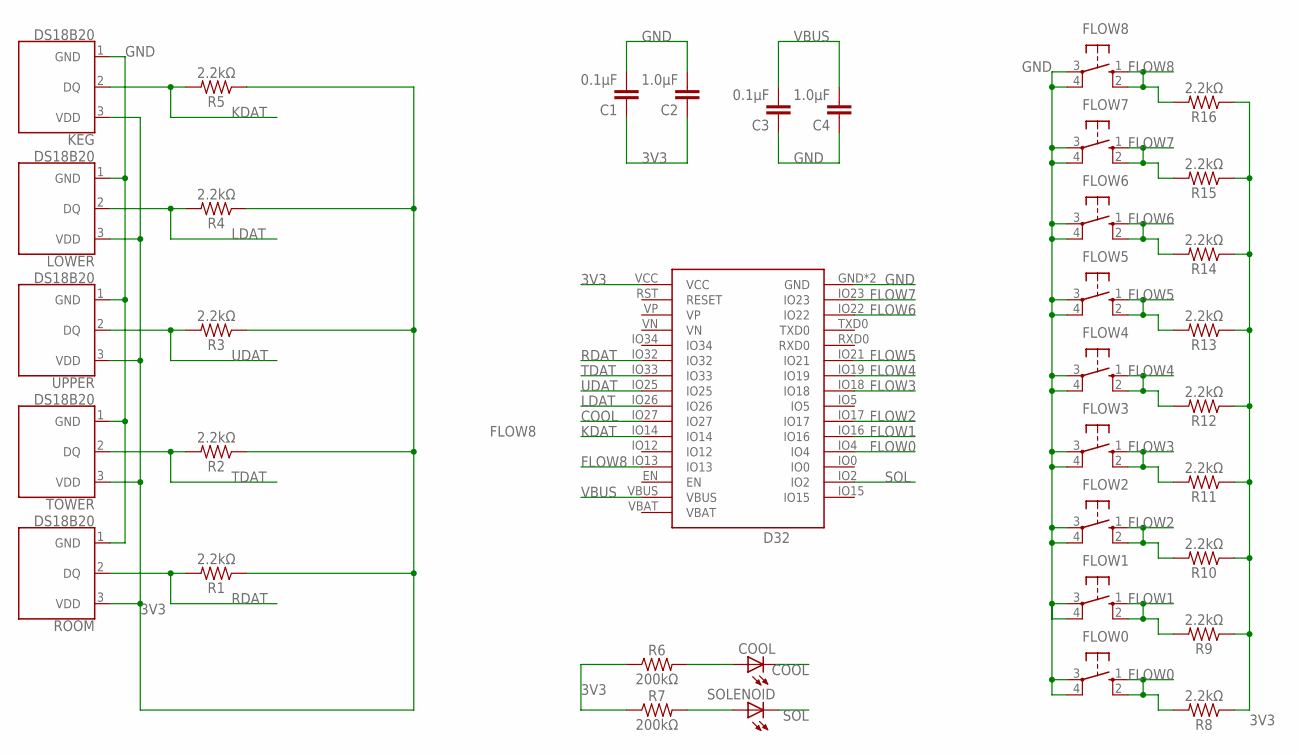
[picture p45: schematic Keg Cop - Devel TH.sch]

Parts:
C1, C3: 0.1μF; CAP_PTH-2.54
C2, C4: 1.0μF; CAP_PTH-2.54
COOL: LED3MM
D32: Lolin D32; D32_NO_BATT
FLOW0, FLOW1, FLOW2, FLOW3, FLOW4, FLOW5, FLOW6, FLOW7, FLOW8: 10-XX; B3F-10XX
KEG: DS18B20; TO-92-AMMO
LOWER: DS18B20; TO-92-AMMO
R1, R2, R3, R4, R5, R8, R9, R10, R11, R12, R13, R14, R15, R16: 2.2kΩ; AXIAL-0.3
R6, R7: 200kΩ; AXIAL-0.3
ROOM: DS18B20; TO-92-AMMO
SOLENOID: LED3MM
TOWER: DS18B20; TO-92-AMMO
UPPER: DS18B20; TO-92-AMMO

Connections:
3V3: C1.1, C2.1, D32.VCC, KEG.3 (VDD), LOWER.3 (VDD), R1.P$1 (1), R2.P$1 (1), R3.P$1 (1), R4.P$1 (1), R5.P$1 (1), R6.P$1 (1), R7.P$1 (1), R8.P$1 (1), R9.P$1 (1), R10.P$1 (1), R11.P$1 (1), R12.P$1 (1), R13.P$1 (1), R14.P$1 (1), R15.P$1 (1), R16.P$1 (1), ROOM.3 (VDD), TOWER.3 (VDD), UPPER.3 (VDD)
COOL: COOL.K (C), D32.IO27
FLOW0: D32.IO4, FLOW0.1 (S), FLOW0.2 (S1), R8.P$2 (2)
FLOW1: D32.IO16, FLOW1.1 (S), FLOW1.2 (S1), R9.P$2 (2)
FLOW2: D32.IO17, FLOW2.1 (S), FLOW2.2 (S1), R10.P$2 (2)
FLOW3: D32.IO18, FLOW3.1 (S), FLOW3.2 (S1), R11.P$2 (2)
FLOW4: D32.IO19, FLOW4.1 (S), FLOW4.2 (S1), R12.P$2 (2)
FLOW5: D32.IO21, FLOW5.1 (S), FLOW5.2 (S1), R13.P$2 (2)
FLOW6: D32.IO22, FLOW6.1 (S), FLOW6.2 (S1), R14.P$2 (2)
FLOW7: D32.IO23, FLOW7.1 (S), FLOW7.2 (S1), R15.P$2 (2)
FLOW8: D32.IO13, FLOW8.1 (S), FLOW8.2 (S1), R16.P$2 (2)
GND: C1.2, C2.2, C3.1, C4.1, D32.GND, D32.GND2 (GND), FLOW0.3, FLOW0.4 (P1), FLOW1.3, FLOW1.4 (P1), FLOW2.3, FLOW2.4 (P1), FLOW3.3, FLOW3.4 (P1), FLOW4.3, FLOW4.4 (P1), FLOW5.3, FLOW5.4 (P1), FLOW6.3, FLOW6.4 (P1), FLOW7.3, FLOW7.4 (P1), FLOW8.3, FLOW8.4 (P1), KEG.1 (GND), LOWER.1 (GND), ROOM.1 (GND), TOWER.1 (GND), UPPER.1 (GND)
KDAT: D32.IO14, KEG.2 (DQ), R5.P$2 (2)
LDAT: D32.IO26, LOWER.2 (DQ), R4.P$2 (2)
unnamed: COOL.A, R6.P$2 (2)
unnamed: R7.P$2 (2), SOLENOID.A
RDAT: D32.IO32, R1.P$2 (2), ROOM.2 (DQ)
SOL: D32.IO2, SOLENOID.K (C)
TDAT: D32.IO33, R2.P$2 (2), TOWER.2 (DQ)
UDAT: D32.IO25, R3.P$2 (2), UPPER.2 (DQ)
VBUS: C3.2, C4.2, D32.VBUS

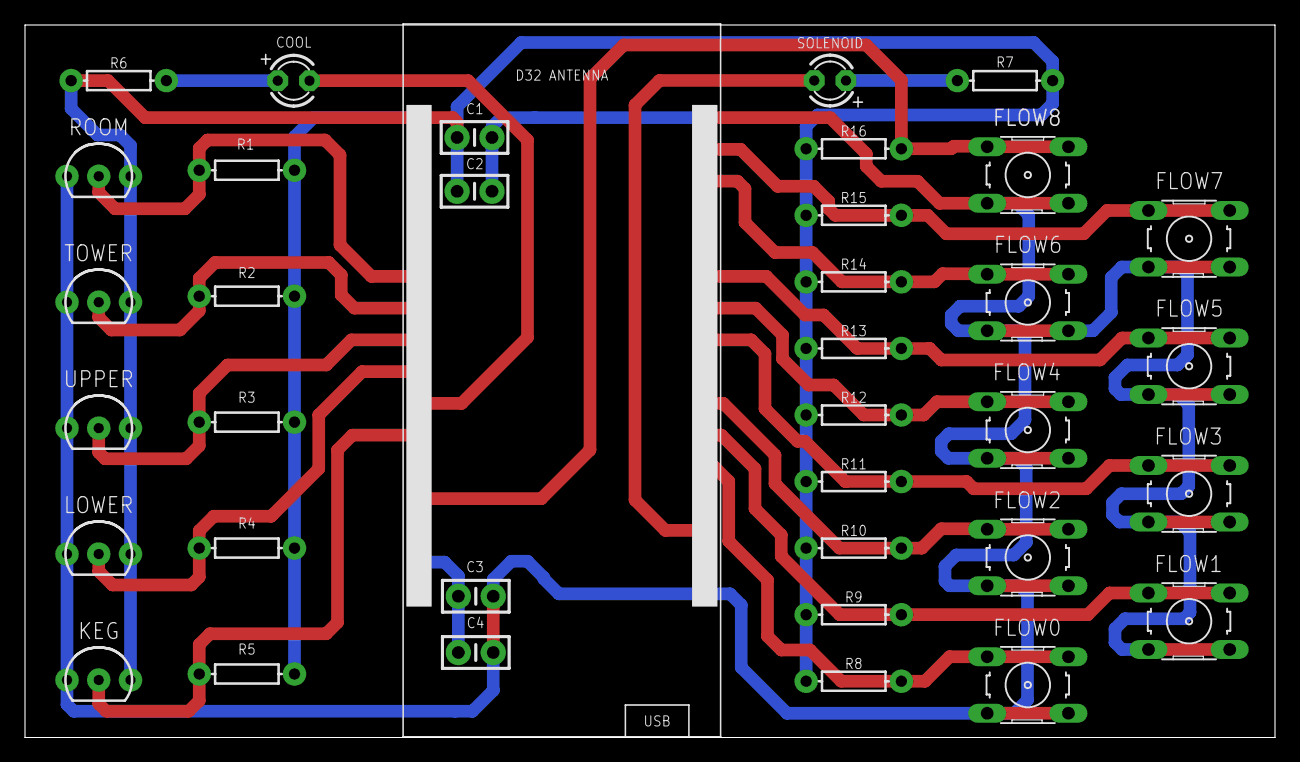
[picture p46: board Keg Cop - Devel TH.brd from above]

Board: 2 copper layers, 100.0 x 57.0 mm, 37 parts (0 on the bottom side), 21 nets.

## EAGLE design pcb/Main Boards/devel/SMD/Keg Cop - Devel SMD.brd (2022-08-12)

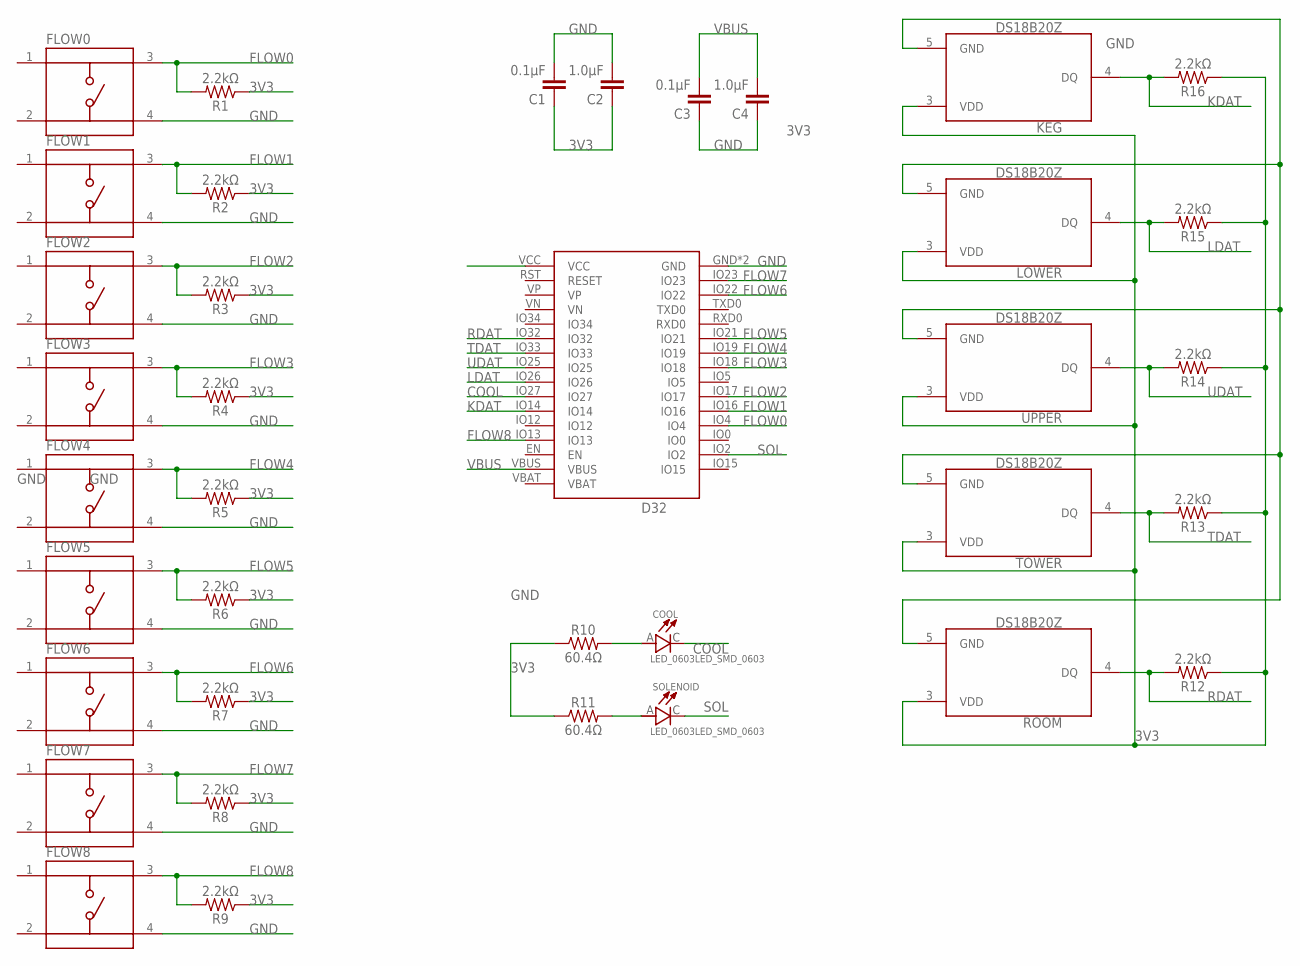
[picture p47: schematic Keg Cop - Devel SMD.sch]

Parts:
C1, C3: 0.1μF; SMD-0805
C2, C4: 1.0μF; SMD-0805
COOL: LED_0603LED_SMD_0603; LED_SMD_0603
D32: Lolin D32; D32_NO_BATT
FLOW0, FLOW1, FLOW2, FLOW3, FLOW4, FLOW5, FLOW6, FLOW7, FLOW8: TS08-66-43-BK-160-SMT-67; SW_TS08-66-43-BK-160-SMT-67
KEG: DS18B20Z; SOIC127P600X175-8N
LOWER: DS18B20Z; SOIC127P600X175-8N
R1, R2, R3, R4, R5, R6, R7, R8, R9, R12, R13, R14, R15, R16: 2.2kΩ; SMD-0805
R10, R11: 60.4Ω; SMD-0805
ROOM: DS18B20Z; SOIC127P600X175-8N
SOLENOID: LED_0603LED_SMD_0603; LED_SMD_0603
TOWER: DS18B20Z; SOIC127P600X175-8N
UPPER: DS18B20Z; SOIC127P600X175-8N

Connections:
3V3: C1.1, C2.1, D32.VCC, KEG.3 (VDD), LOWER.3 (VDD), R1.1, R2.1, R3.1, R4.1, R5.1, R6.1, R7.1, R8.1, R9.1, R10.1, R11.1, R12.1, R13.1, R14.1, R15.1, R16.1, ROOM.3 (VDD), TOWER.3 (VDD), UPPER.3 (VDD)
COOL: COOL.C, D32.IO27
FLOW0: D32.IO4, FLOW0.3, R1.2
FLOW1: D32.IO16, FLOW1.3, R2.2
FLOW2: D32.IO17, FLOW2.3, R3.2
FLOW3: D32.IO18, FLOW3.3, R4.2
FLOW4: D32.IO19, FLOW4.3, R5.2
FLOW5: D32.IO21, FLOW5.3, R6.2
FLOW6: D32.IO22, FLOW6.3, R7.2
FLOW7: D32.IO23, FLOW7.3, R8.2
FLOW8: D32.IO13, FLOW8.3, R9.2
GND: C1.2, C2.2, C3.1, C4.1, D32.GND, D32.GND2 (GND), FLOW0.4, FLOW1.4, FLOW2.4, FLOW3.4, FLOW4.4, FLOW5.4, FLOW6.4, FLOW7.4, FLOW8.4, KEG.5 (GND), LOWER.5 (GND), ROOM.5 (GND), TOWER.5 (GND), UPPER.5 (GND)
KDAT: D32.IO14, KEG.4 (DQ), R16.2
LDAT: D32.IO26, LOWER.4 (DQ), R15.2
unnamed: COOL.A, R10.2
unnamed: R11.2, SOLENOID.A
RDAT: D32.IO32, R12.2, ROOM.4 (DQ)
SOL: D32.IO2, SOLENOID.C
TDAT: D32.IO33, R13.2, TOWER.4 (DQ)
UDAT: D32.IO25, R14.2, UPPER.4 (DQ)
VBUS: C3.2, C4.2, D32.VBUS

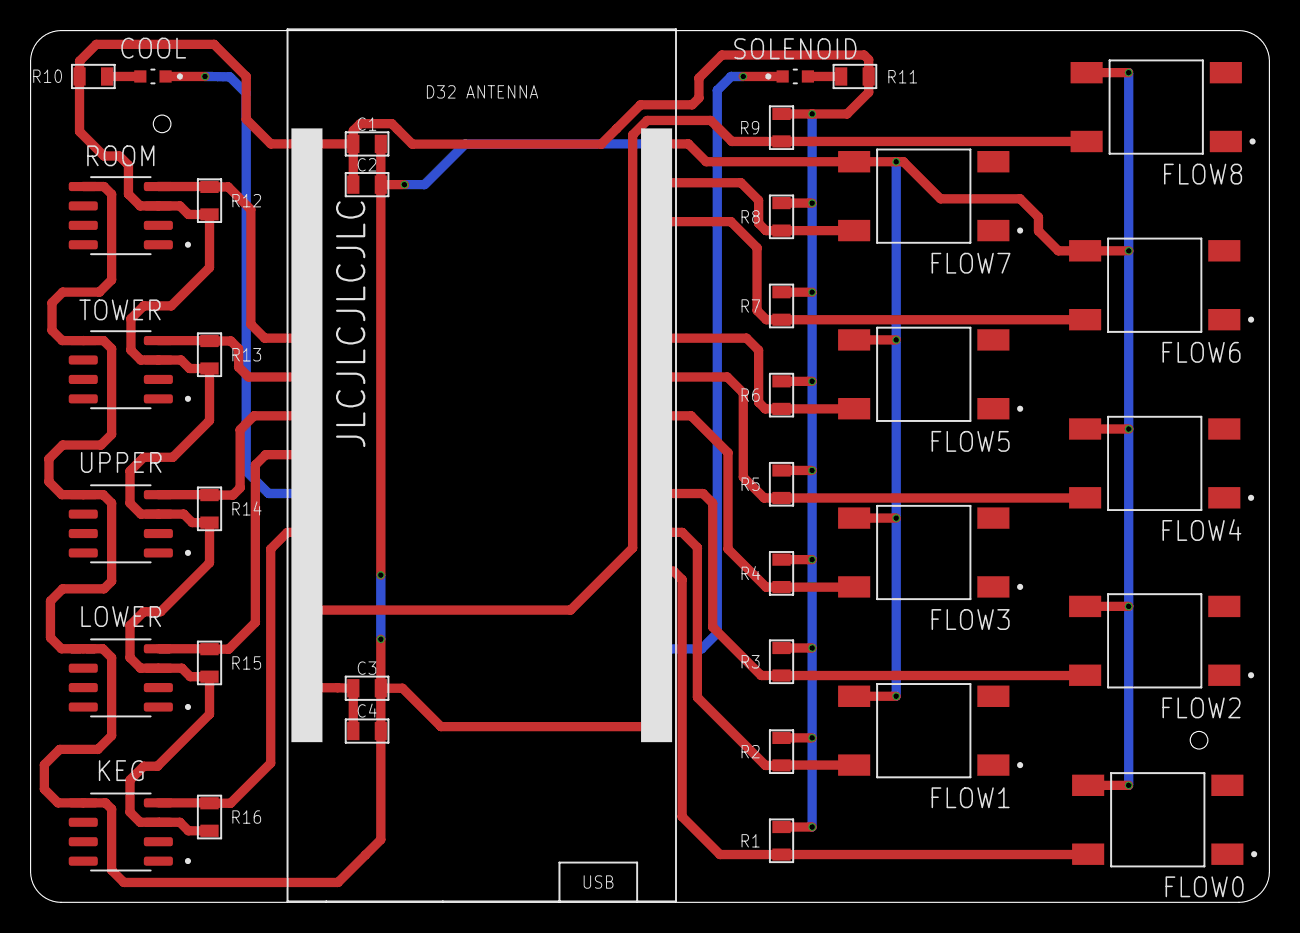
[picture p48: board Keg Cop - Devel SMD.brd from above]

Board: 2 copper layers, 81.0 x 57.0 mm, 39 parts (0 on the bottom side), 21 nets.

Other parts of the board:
U$1, U$2: 1.152

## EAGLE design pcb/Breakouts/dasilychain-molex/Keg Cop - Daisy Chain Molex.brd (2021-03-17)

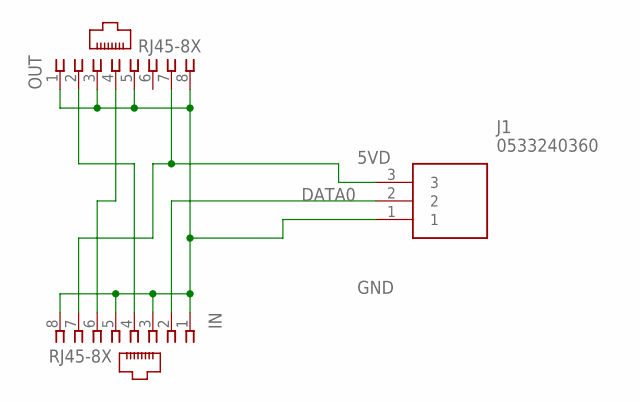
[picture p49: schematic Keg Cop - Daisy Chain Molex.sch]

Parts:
IN: RJ45-8X; RJ45-NO-SHIELD
J1: 0533240360
OUT: RJ45-8X; RJ45-NO-SHIELD

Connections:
5VD: IN.7, J1.3, OUT.7
DATA0: IN.2, J1.2
DATA1: IN.4, OUT.2
DATA2: IN.6, OUT.4
GND: IN.1, IN.3, IN.5, IN.8, J1.1, OUT.1, OUT.3, OUT.5, OUT.8

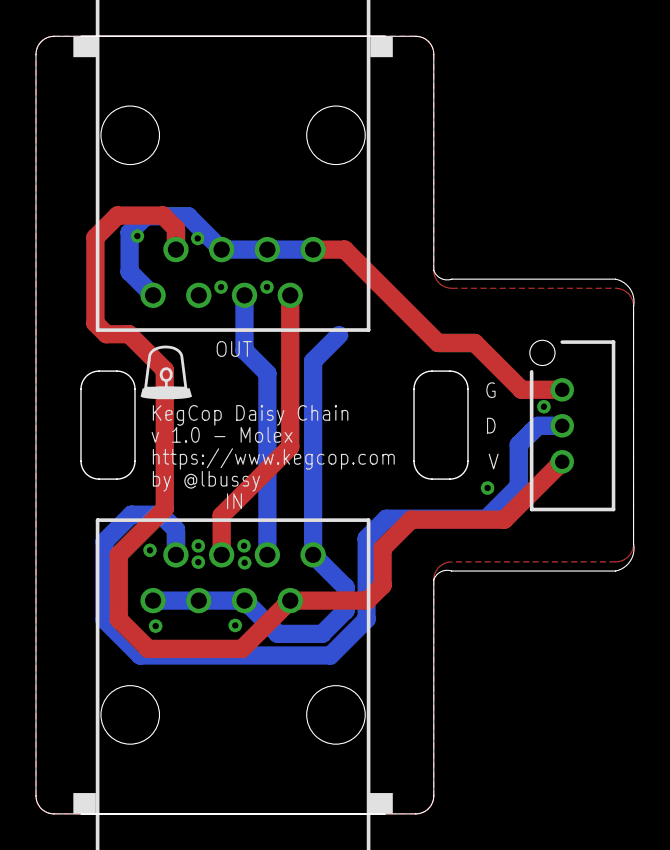
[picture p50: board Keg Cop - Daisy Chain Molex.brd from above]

Board: 2 copper layers, 33.2 x 43.2 mm, 3 parts (0 on the bottom side), 5 nets.

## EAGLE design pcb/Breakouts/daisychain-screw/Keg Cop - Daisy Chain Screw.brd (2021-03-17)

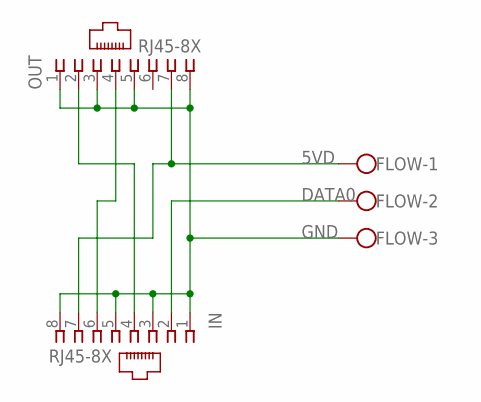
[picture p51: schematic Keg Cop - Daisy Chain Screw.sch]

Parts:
FLOW: W237-103
IN: RJ45-8X; RJ45-NO-SHIELD
OUT: RJ45-8X; RJ45-NO-SHIELD

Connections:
5VD: FLOW.1, IN.7, OUT.7
DATA0: FLOW.2, IN.2
DATA1: IN.4, OUT.2
DATA2: IN.6, OUT.4
GND: FLOW.3, IN.1, IN.3, IN.5, IN.8, OUT.1, OUT.3, OUT.5, OUT.8

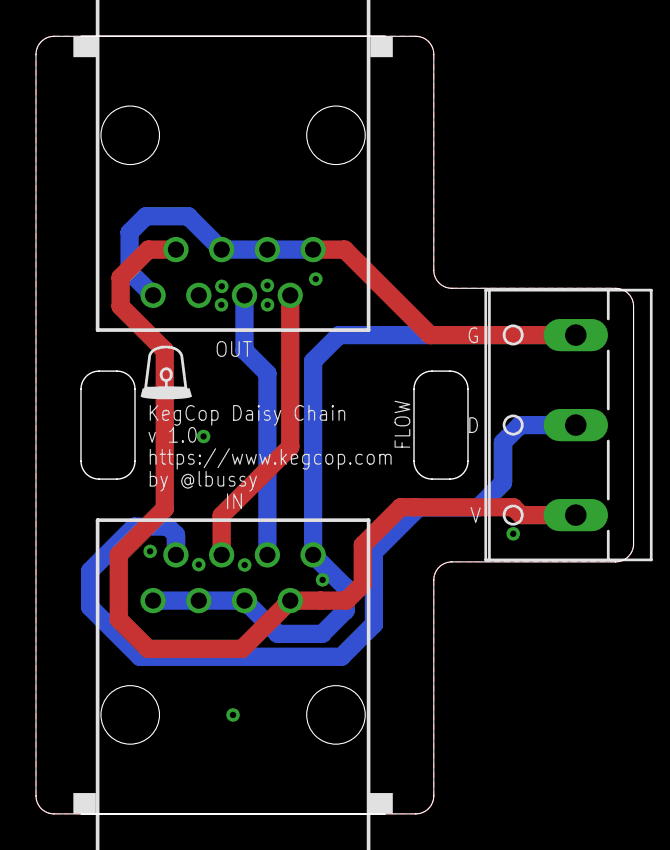
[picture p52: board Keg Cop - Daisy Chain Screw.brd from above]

Board: 2 copper layers, 33.2 x 43.2 mm, 3 parts (0 on the bottom side), 5 nets.

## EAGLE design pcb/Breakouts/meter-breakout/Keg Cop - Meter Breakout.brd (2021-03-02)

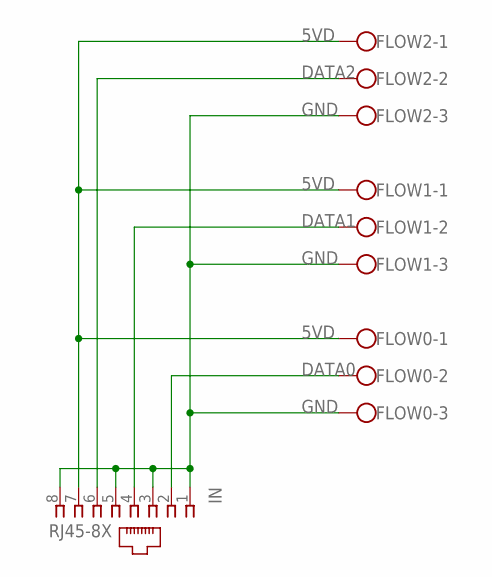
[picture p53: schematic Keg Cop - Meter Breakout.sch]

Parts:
FLOW0, FLOW1, FLOW2: W237-103
IN: RJ45-8X; RJ45-NO-SHIELD

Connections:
5VD: FLOW0.1, FLOW1.1, FLOW2.1, IN.7
DATA0: FLOW0.2, IN.2
DATA1: FLOW1.2, IN.4
DATA2: FLOW2.2, IN.6
GND: FLOW0.3, FLOW1.3, FLOW2.3, IN.1, IN.3, IN.5, IN.8

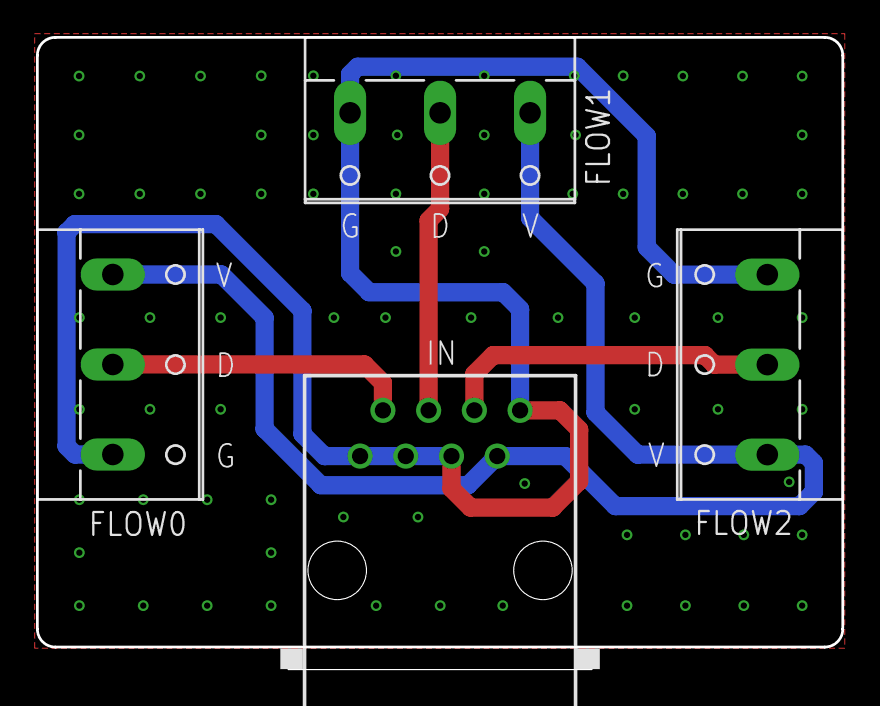
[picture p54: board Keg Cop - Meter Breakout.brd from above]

Board: 2 copper layers, 44.7 x 35.1 mm, 4 parts (0 on the bottom side), 5 nets.

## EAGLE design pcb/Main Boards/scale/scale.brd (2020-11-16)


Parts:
C1, C3, C5, C6, C7: 0.1μF; CAP_PTH-2.54
C2, C4, C8: 1.0μF; CAP_PTH-2.54
C9: 330pF; CAP_PTH-2.54
D32: Lolin D32; D32_NO_BATT
IC1: DS18B20+; TO-92
J1: 691321300004; SHDR4W80P0X381_1X4_1643X720X92
POWER: 2-PIN; HDR-2_VERT
R1, R2, R3, R4, R5, R8, R9: 2.2kΩ; AXIAL-0.3
R6, R7: 47Ω; AXIAL-0.3
RELAY: 4-PIN; MA04-1
ROOM: 3-PIN; HDR-3_VERT
U1: NAU7802; DIP16
X1: RJ45-8X; RJ45-NO-SHIELD

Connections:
3V3: C1.1, C2.1, D32.VCC, R1.P$1 (1), R2.P$1 (1), R3.P$1 (1), R4.P$1 (1), R5.P$1 (1), R8.P$2 (2), R9.P$2 (2), RELAY.4, U1.15 (DVDD)
5V: C3.1, C4.1, D32.VBUS, IC1.3 (VDD), POWER.2, ROOM.2, X1.8
A+: J1.3, R7.P$1 (1)
A-: J1.4, R6.P$1 (1)
B+: C9.2, U1.5 (VIN2P)
COOL: RELAY.3
GND: C1.2, C2.2, C3.2, C4.2, C6.2, C7.1, C8.2, D32.GND, D32.GND2 (GND), IC1.1 (GND), J1.2, POWER.1, RELAY.1, ROOM.1, U1.7 (REFN), U1.8 (AVSS), U1.9 (DVSS), X1.7
KDAT: D32.IO21, R5.P$2 (2), X1.5, X1.6
LDAT: D32.IO19, R4.P$2 (2), X1.4
LED: D32.IO5
unnamed: C9.1, U1.4 (VIN2N)
unnamed: C7.2, U1.6 (VBG)
unnamed: C5.2, R7.P$2 (2), U1.3 (VIN1P)
unnamed: C5.1, R6.P$2 (2), U1.2 (VIN1N)
RDAT: D32.IO16, IC1.2 (DQ), R1.P$2 (2), ROOM.3, X1.1
SCL: D32.IO26, R8.P$1 (1), U1.13 (SCLK)
SDA: D32.IO25, R9.P$1 (1), U1.14 (SDIO)
SOL: RELAY.2
TDAT: D32.IO17, R2.P$2 (2), X1.2
TFT_BL: D32.IO32
TFT_CS: D32.IO14
TFT_DC: D32.IO27
TFT_RST: D32.IO33
TS_CS: D32.IO12
UDAT: D32.IO18, R3.P$2 (2), X1.3
VDDA: C6.1, C8.1, J1.1, U1.1 (REFP), U1.16 (AVDD)
WIFI_RST: D32.IO13

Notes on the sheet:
NAU7802
Scale Interface
1 - Red - VDDA 2 - Black - GND 3 - White - A- 4 - Green - A+


Board: 2 copper layers, 65.1 x 51.2 mm, 29 parts (0 on the bottom side), 18 nets.

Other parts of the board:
U$1, U$2, U$3: 3,0

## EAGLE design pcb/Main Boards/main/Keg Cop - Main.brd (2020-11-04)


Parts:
C1, C3: 0.1μF; CAP_PTH-2.54
C2, C4: 1.0μF; CAP_PTH-2.54
D32: Lolin D32; D32_NO_BATT
IC1: DS18B20+; TO-92
POWER: 2-PIN; HDR-2_VERT
R1, R2, R3, R4, R5, R6, R7, R8, R9, R10, R11, R12, R13, R14: 2.2kΩ; AXIAL-0.3
RELAY: 4-PIN; MA04-1
ROOM: 3-PIN; HDR-3_VERT
X1, X2, X3, X4: RJ45-8X; RJ45-NO-SHIELD

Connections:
3V3: C1.1, C2.1, D32.VCC, R1.P$1 (1), R2.P$1 (1), R3.P$1 (1), R4.P$1 (1), R5.P$1 (1), R6.P$2 (2), R7.P$2 (2), R8.P$2 (2), R9.P$2 (2), R10.P$2 (2), R11.P$2 (2), R12.P$2 (2), R13.P$2 (2), R14.P$2 (2), RELAY.4
5V: C3.1, C4.1, D32.VBUS, IC1.3 (VDD), POWER.2, ROOM.2, X1.8, X2.7, X3.7, X4.7
COOL: D32.IO27, RELAY.3
GND: C1.2, C2.2, C3.2, C4.2, D32.GND, D32.GND2 (GND), IC1.1 (GND), POWER.1, RELAY.1, ROOM.1, X1.7, X2.1, X2.3, X2.5, X2.8, X3.1, X3.3, X3.5, X3.8, X4.1, X4.3, X4.5, X4.8
KDAT: D32.IO14, R5.P$2 (2), X1.5, X1.6
KEG0: D32.IO4, R14.P$1 (1), X2.2
KEG1: D32.IO16, R13.P$1 (1), X2.4
KEG2: D32.IO17, R12.P$1 (1), X2.6
KEG3: D32.IO18, R11.P$1 (1), X3.2
KEG4: D32.IO19, R10.P$1 (1), X3.4
KEG5: D32.IO21, R9.P$1 (1), X3.6
KEG6: D32.IO22, R8.P$1 (1), X4.2
KEG7: D32.IO23, R7.P$1 (1), X4.4
KEG8: D32.IO13, R6.P$1 (1), X4.6
LDAT: D32.IO26, R4.P$2 (2), X1.4
RDAT: D32.IO32, IC1.2 (DQ), R1.P$2 (2), ROOM.3, X1.1
SOL: D32.IO2, RELAY.2
TDAT: D32.IO33, R2.P$2 (2), X1.2
UDAT: D32.IO25, R3.P$2 (2), X1.3


Board: 2 copper layers, 65.0 x 55.5 mm, 30 parts (0 on the bottom side), 19 nets.

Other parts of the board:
U$1, U$2, U$3: 3,0

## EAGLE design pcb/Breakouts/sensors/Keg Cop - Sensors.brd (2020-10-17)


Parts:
KDAT: W237-103
LDAT: W237-103
SENSORS: RJ45-8X; RJ45-NO-SHIELD
TDAT: W237-103
UDAT: W237-103

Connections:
5V: KDAT.2, LDAT.2, SENSORS.8, TDAT.2, UDAT.2
GND: KDAT.1, LDAT.1, SENSORS.7, TDAT.1, UDAT.1
KDAT: KDAT.3, SENSORS.5, SENSORS.6
LDAT: LDAT.3, SENSORS.4
TDAT: SENSORS.2, TDAT.3
UDAT: SENSORS.3, UDAT.3


Board: 2 copper layers, 45.8 x 33.3 mm, 6 parts (0 on the bottom side), 6 nets.

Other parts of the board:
U$1: 3,0

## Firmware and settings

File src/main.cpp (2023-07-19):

/* Copyright (C) 2019-2023 Lee C. Bussy (@LBussy)

This file is part of Lee Bussy's Keg Cop (keg-cop).

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
THE SOFTWARE IS PROVIDED "AS IS", WITHOUT WARRANTY OF ANY KIND, EXPRESS OR
IMPLIED, INCLUDING BUT NOT LIMITED TO THE WARRANTIES OF MERCHANTABILITY,
FITNESS FOR A PARTICULAR PURPOSE AND NONINFRINGEMENT. IN NO EVENT SHALL THE
AUTHORS OR COPYRIGHT HOLDERS BE LIABLE FOR ANY CLAIM, DAMAGES OR OTHER
LIABILITY, WHETHER IN AN ACTION OF CONTRACT, TORT OR OTHERWISE, ARISING FROM,
OUT OF OR IN CONNECTION WITH THE SOFTWARE OR THE USE OR OTHER DEALINGS IN THE
SOFTWARE. */

#include "main.h"

#include "thatVersion.h"
#include "kegscreen.h"
#include "appconfig.h"
#include "serialhandler.h"
#include "config.h"
#include "ntphandler.h"
#include "wifihandler.h"
#include "webpagehandler.h"
#include "version.h"
#include "mdnshandler.h"
#include "tempsensors.h"
#include "thermostat.h"
#include "flowmeter.h"
#include "tools.h"
#include "execota.h"
#include "uptimelog.h"
#include "taplistio.h"
#include "flowconfig.h"
#include "homeassist.h"

#include <ArduinoLog.h>
#include <ESP_DoubleResetDetector.h>
#include <Ticker.h>

DoubleResetDetector *drd;

Ticker pollSensorsTicker;
Ticker doControlTicker;
Ticker doFanControlTicker;
Ticker logPourTicker;
Ticker getThatVersionTicker;
Ticker sendKSTempReportTicker;
Ticker sendTargetReportTicker;
Ticker sendHASSDiscovery;
Ticker sendHASSAvailability;
Ticker sendHASSState;

void setup()
{
    if (!FILESYSTEM.begin(false, "/spiffs", 32))
        playDead("filesystem");

    drd = new DoubleResetDetector(DRD_TIMEOUT, DRD_ADDRESS);

    if (!loadAppConfig(APP_FILENAME))
        playDead("App config");

    serialBegin();

    // Set wifi reset pin
    pinMode(RESETWIFI, INPUT_PULLUP);
    // Set LED pin
    pinMode(LED, OUTPUT);

    // Set pins for relays
    pinMode(SOLENOID, OUTPUT);
    if (app.temps.tfancontrolenabled)
    {
        digitalWrite(SOLENOID, (app.temps.tfanonhigh) ? LOW : HIGH);
    }
    else
    {
        digitalWrite(SOLENOID, (app.copconfig.tapsolenoid) ? LOW : HIGH);
    }
    pinMode(COOL, OUTPUT);
    digitalWrite(COOL, (app.temps.coolonhigh) ? LOW : HIGH);

    // Initialize flowmeters before checking for FILESYSTEM update
    if (!initFlow())
    { // If flowmeter configuration does not load, sit and blink slowly like an idiot
        pinMode(LED, OUTPUT);
        Ticker blinker;
        blinker.attach_ms(CONFIGBLINK, []()
                          { digitalWrite(LED, !(digitalRead(LED))); });
        while (true)
        {
        };
    }

    // Clear temperature sensor emulation
    app.copconfig.tempemulate = false;

    // Clear all tap calibration
    app.copconfig.pouremulate = false;
    for (int i = 0; i < NUMTAPS; i++)
    {
        flow.taps[i].calibrating = false;
    }
    setDoSaveApp();
    setDoSaveFlow();

    // Check if portal is requested
    bool detectdrd = drd->detectDoubleReset();
    if (!app.copconfig.nodrd && detectdrd)
    {
        Log.notice(F("DRD: Portal requested." CR));
        killDRD();
        doWiFi(true);
    }
    else if (digitalRead(RESETWIFI) == LOW)
    {
        Log.notice(F("Pin %d low, presenting portal." CR), RESETWIFI);
        killDRD();
        doWiFi(true);
    }
    else
    {
        Log.notice(F("Starting WiFi." CR));
        app.copconfig.nodrd = false;
        doWiFi();
    }

    setClock(); // Set NTP Time

    if (!app.ota.badfw)
        execspiffs(); // Check for pending FILESYSTEM update

    mDNSStart();                 // Set up mDNS responder
    startWebServer();            // Turn on web server
    sensorInit();                // Initialize temperature sensors
    startTstat(TS_TYPE_CHAMBER); // Initialize temperature control
    startTstat(TS_TYPE_TOWER);   // Initialize fan control
    doVersionPoll();             // Get server version at startup
    doKSJSON();                  // Add KegScreen TV configuration
#ifdef _DEBUG_BUILD
    doUptime(true); // Uptime log start
#endif

    // Setup tickers
    pollSensorsTicker.attach(TEMPLOOP, pollTemps);                                  // Poll temperature sensors
    logPourTicker.attach(TAPLOOP, logFlow);                                         // Log pours
    getThatVersionTicker.attach(POLLSERVERVERSION, doVersionPoll);                  // Poll for server version
    sendKSTempReportTicker.attach(KSTEMPREPORT + random(1, 20), setDoKSTempReport); // Send KegScreen Temp Report
    sendTargetReportTicker.attach(app.urltarget.freq * 60, setDoTargetReport);      // Send Target Report
    doControlTicker.attach(TEMPLOOP, []()
                           { loopTstat(TS_TYPE_CHAMBER); }); // Update temperature control loop
    doFanControlTicker.attach(TEMPLOOP, []()
                              { loopTstat(TS_TYPE_TOWER); }); // Update fan control loop

#if !defined(DISABLE_LOGGING)
    if (app.copconfig.serial)
        nullDoc("d");
    else
        Log.notice(F("Started %s version %s/%s (%s) [%s]." CR), AppKeys::appname, fw_version(), fs_version(), branch(), build());
#else
    nullDoc("d");
#endif
    sendTIOTaps();                                   // Send initial Taplist.io keg levels
    sendHASSDiscovery.attach(5, queueHASSDiscov);    // Queue all HASS discovery and send on timer
    sendHASSAvailability.attach(30, queueHASSAvail); // Queue all HASS availability and send on timer
    sendHASSState.attach(40, queueHASSState);        // Queue all HASS states and send on timer
}

void loop()
{
    if (!wifiPause)
    {
        // Check for Target URL Timing reset
        if (app.urltarget.update)
        {
            Log.notice(F("Resetting URL Target frequency timer to %l minutes." CR), app.urltarget.freq);
            sendTargetReportTicker.detach();
            sendTargetReportTicker.attach(app.urltarget.freq * 60, setDoTargetReport);
            app.urltarget.update = false;
        }

        doOTALoop();
        tickerLoop();
        drd->loop();
        serialLoop();
        maintenanceLoop();
        doHASSLoop();
    }
}

void stopMainProc()
{
    Log.notice(F("Stopping all main loop timers and filesystem." CR));
    FILESYSTEM.end();
    pollSensorsTicker.detach();
    logPourTicker.detach();
    getThatVersionTicker.detach();
    sendKSTempReportTicker.detach();
    sendTargetReportTicker.detach();
    doControlTicker.detach();
    doFanControlTicker.detach();
}

void startMainProc()
{
    Log.verbose(F("Starting all main loop timers and filesystem" CR));
    pollSensorsTicker.attach(TEMPLOOP, pollTemps);                             // Poll temperature sensors
    logPourTicker.attach(TAPLOOP, logFlow);                                    // Log pours
    getThatVersionTicker.attach(POLLSERVERVERSION, doVersionPoll);             // Poll for server version
    sendKSTempReportTicker.attach(KSTEMPREPORT, setDoKSTempReport);            // Send KegScreen Temp Report
    sendTargetReportTicker.attach(app.urltarget.freq * 60, setDoTargetReport); // Send Target Report
    doControlTicker.attach(TEMPLOOP, []()
                           { loopTstat(TS_TYPE_CHAMBER); }); // Update temperature control loop
    doFanControlTicker.attach(TEMPLOOP, []()
                              { loopTstat(TS_TYPE_TOWER); }); // Update fan control loop
}

void playDead(String cause = "")
{
    if (!Serial)
    {
        Serial.begin(BAUD);
        while (!Serial)
        {
            ;
        }
        Serial.flush();
        Serial.println();
    }
    if (cause.length() > 1)
        Serial.printf("Fatal error in %s, stopping \n"), cause;
    else
        Serial.println(F("Fatal error, stopping."));
    pinMode(LED, OUTPUT);
    Ticker blinker;
    blinker.attach_ms(CONFIGBLINK, []()
                      { digitalWrite(LED, !(digitalRead(LED))); });
}

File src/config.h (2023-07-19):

/* Copyright (C) 2019-2023 Lee C. Bussy (@LBussy)

This file is part of Lee Bussy's Keg Cop (keg-cop).

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
THE SOFTWARE IS PROVIDED "AS IS", WITHOUT WARRANTY OF ANY KIND, EXPRESS OR
IMPLIED, INCLUDING BUT NOT LIMITED TO THE WARRANTIES OF MERCHANTABILITY,
FITNESS FOR A PARTICULAR PURPOSE AND NONINFRINGEMENT. IN NO EVENT SHALL THE
AUTHORS OR COPYRIGHT HOLDERS BE LIABLE FOR ANY CLAIM, DAMAGES OR OTHER
LIABILITY, WHETHER IN AN ACTION OF CONTRACT, TORT OR OTHERWISE, ARISING FROM,
OUT OF OR IN CONNECTION WITH THE SOFTWARE OR THE USE OR OTHER DEALINGS IN THE
SOFTWARE. */

#ifndef CONFIG_H
#define CONFIG_H

#include <LittleFS.h>

//////////////////////////////////////////////////////////////////////////
//
// Stringify Defines
//
#define stringify(s) _stringifyDo(s)
#define _stringifyDo(s) #s
//
//////////////////////////////////////////////////////////////////////////

//////////////////////////////////////////////////////////////////////////
//
// Define App Name (identifies application to target)
//
#ifndef APP_NAME
#define APP_NAME "Keg Cop"
#endif
//
//////////////////////////////////////////////////////////////////////////

//////////////////////////////////////////////////////////////////////////
//
// Define API_V1 Key (identifies application to target)
//
#ifndef API_KEY
#define API_KEY "keg_cop"
#endif
//
//////////////////////////////////////////////////////////////////////////

//////////////////////////////////////////////////////////////////////////
//
// Keg Cop's default theme
//
#ifndef THEME
#define THEME "cerulean"
#endif
//
//////////////////////////////////////////////////////////////////////////

//////////////////////////////////////////////////////////////////////////
//
// Define Keg Cop's filesystem
//
#ifndef FILESYSTEM
#define FILESYSTEM LittleFS
#endif
//
//////////////////////////////////////////////////////////////////////////

//////////////////////////////////////////////////////////////////////////
//
// Set verbosity of debug messages 0-6
//
//      * 0 - LOG_LEVEL_SILENT     no output
//      * 1 - LOG_LEVEL_FATAL      fatal errors
//      * 2 - LOG_LEVEL_ERROR      all errors
//      * 3 - LOG_LEVEL_WARNING    errors, and warnings
//      * 4 - LOG_LEVEL_NOTICE     errors, warnings and notices
//      * 5 - LOG_LEVEL_TRACE      errors, warnings, notices & traces
//      * 6 - LOG_LEVEL_VERBOSE    all
//
// Uncomment #define for logging level desired.
//
#ifndef LOG_LEVEL
#ifdef _DEBUG_BUILD
#define LOG_LEVEL LOG_LEVEL_NOTICE
#else
#define LOG_LEVEL LOG_LEVEL_NOTICE // Errors, warnings and notices
#endif
// #define DISABLE_LOGGING
// #define LOG_LEVEL LOG_LEVEL_SILENT     // No output
// #define LOG_LEVEL LOG_LEVEL_FATAL      // Fatal errors
// #define LOG_LEVEL LOG_LEVEL_ERROR      // All errors
// #define LOG_LEVEL LOG_LEVEL_WARNING    // Errors, and warnings
// #define LOG_LEVEL LOG_LEVEL_NOTICE     // Errors, warnings and notices
// #define LOG_LEVEL LOG_LEVEL_TRACE      // Errors, warnings, notices & traces
// #define LOG_LEVEL LOG_LEVEL_VERBOSE    // All
#endif
//
//////////////////////////////////////////////////////////////////////////

//////////////////////////////////////////////////////////////////////////
//
// Double Reset Detect Configuration
// https://github.com/khoih-prog/ESP_DoubleResetDetector/
//
#ifndef DRD_TIMEOUT
#define ESP_DRD_USE_LITTLEFS true
#define DOUBLERESETDETECTOR_DEBUG false
#define DRD_TIMEOUT 5
#define DRD_ADDRESS 0 // Not used for FILESYSTEM, still needed for init
#endif
//
//////////////////////////////////////////////////////////////////////////

//////////////////////////////////////////////////////////////////////////
//
// Echo all serial output to telnet
//
#ifndef TELNETPORT
#define TELNETPORT 23
#endif
//
//////////////////////////////////////////////////////////////////////////

//////////////////////////////////////////////////////////////////////////
//
// Reset controller every XX days (in millis)
//
#ifndef ESPREBOOT
#define ESPREBOOT (unsigned long) 42 * 24 * 60 * 60 * 1000 // Reboot every 42 days
#endif
//
//////////////////////////////////////////////////////////////////////////

//////////////////////////////////////////////////////////////////////////
//
// Reset NTP every 24 hours
//
#ifndef NTPRESET
#define NTPRESET (unsigned long) 24 * 60 * 60 * 1000
#endif
//
//////////////////////////////////////////////////////////////////////////

//////////////////////////////////////////////////////////////////////////
//
// Timer for HASS Availability
//
#ifndef HASSUPDATE
#define HASSUPDATE 5 * 60
#endif
//
//////////////////////////////////////////////////////////////////////////

//////////////////////////////////////////////////////////////////////////
//
// Minumum Free Heap, triggers reset if below this value
//
#ifndef MINFREEHEAP
#define MINFREEHEAP (unsigned long)10000
#endif
//
//////////////////////////////////////////////////////////////////////////
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

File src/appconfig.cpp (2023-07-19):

/* Copyright (C) 2019-2023 Lee C. Bussy (@LBussy)

This file is part of Lee Bussy's Keg Cop (keg-cop).

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
THE SOFTWARE IS PROVIDED "AS IS", WITHOUT WARRANTY OF ANY KIND, EXPRESS OR
IMPLIED, INCLUDING BUT NOT LIMITED TO THE WARRANTIES OF MERCHANTABILITY,
FITNESS FOR A PARTICULAR PURPOSE AND NONINFRINGEMENT. IN NO EVENT SHALL THE
AUTHORS OR COPYRIGHT HOLDERS BE LIABLE FOR ANY CLAIM, DAMAGES OR OTHER
LIABILITY, WHETHER IN AN ACTION OF CONTRACT, TORT OR OTHERWISE, ARISING FROM,
OUT OF OR IN CONNECTION WITH THE SOFTWARE OR THE USE OR OTHER DEALINGS IN THE
SOFTWARE. */

#include "appconfig.h"

#include "tools.h"
#include "serialhandler.h"

#include <FS.h>
#include <LittleFS.h>
#include <ArduinoLog.h>

AppConfig app;

#define APP_DEBUG_LOG "/appdebuglog.txt"
bool appLoadError = false;

const char *appConfig = "[APPCONFIG]";

bool loadAppConfig(const char *filename)
{
    return loadAppConfig(filename, false);
}

bool loadAppConfig(const char *filename, bool isBackup)
{
    Log.notice(F("%s Loading configuration." CR), appConfig);
    bool loadOK = false;
    bool loadedBackup = false;

    // Loads the configuration from a file on FILESYSTEM
    File file = FILESYSTEM.open(filename, FILE_READ);
    if (!FILESYSTEM.exists(filename) || !file)
    {
        Log.error(F("%s configuration %s does not exist." CR), appConfig, filename);
        appLoadError = true;
        debugAppLog(false);
        loadOK = false;
    }
    else if (!deserializeAppConfig(file))
    {
        Log.error(F("%s Failed to load %s from filesystem." CR), appConfig, filename);
        appLoadError = true;
        debugAppLog(true);
        loadOK = false;
    }
    else
    {
        loadOK = true;
    }
    file.close();

    if (!loadOK && !isBackup) // We're only partially screwed, maybe
    {
        if (!loadAppConfig(APP_FILENAME_BACKUP, true)) // Try with the backup file
        {
            Log.error(F("%s Failed to load configuration from backup, creating from defaults." CR), appConfig);
            saveAppConfig(APP_FILENAME);
        }
        else
        {
            // We ripped success from the jaws of defeat with cutting edge-code
            Log.notice(F("%s Sucessfully loaded configuration fro backup." CR), appConfig);
            saveAppConfig(APP_FILENAME);
            loadOK = true;
        }
    }

    Log.trace(F("%s Configuration load complete." CR), appConfig);
    appLoadError = false;
    return loadOK;
}

bool saveAppConfig(const char * filename)
{
    Log.notice(F("%s Save: Saving configuration." CR), AppKeys::appname);
    bool retval = false;

    // Saves the configuration to a file on FILESYSTEM
    File file = FILESYSTEM.open(filename, FILE_WRITE);
    if (!file)
    {
        Log.error(F("%s Save: Unable to open or create file, partition may be corrupt." CR), AppKeys::appname);
        retval = false;
    }
    // Serialize JSON to file
    else if (!serializeAppConfig(file))
    {
        Log.error(F("%s Save: Failed to save configuration, data may be lost." CR), AppKeys::appname);
        retval = false;
    }
    else
    {
        Log.trace(F("%s Save: Configuration saved." CR), AppKeys::appname);
        retval = true;
    }
    file.close();
    if (retval)
    {
        copyFile(APP_FILENAME, APP_FILENAME_BACKUP);
    }
    return retval;
}

bool deserializeAppConfig(Stream &src)
{
    // Deserialize configuration
    DynamicJsonDocument doc(CAPACITY_APP_DESERIAL);

    // Parse the JSON object in the file
    DeserializationError err = deserializeJson(doc, src);

    if (err)
    {
        app.load(doc.as<JsonObject>());
        return true;
    }
    else
    {
        app.load(doc.as<JsonObject>());
        return true;
    }
}

bool serializeAppConfig(Print &dst)
{
    // Serialize configuration
    DynamicJsonDocument doc(CAPACITY_APP_SERIAL);

    // Create an object at the root
    JsonObject root = doc.to<JsonObject>();

    // Fill the object
    app.save(root);

    // Serialize JSON to file
    return serializeJsonPretty(doc, dst) > 0;
}

void ApConfig::save(JsonObject obj) const
{
    obj[AppKeys::ssid] = ssid;
    obj[AppKeys::passphrase] = passphrase;
}
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

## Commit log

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2019-12-30 New board files
    [Keg Cop - Daisy Chain RJ45 T with Slots.brd, Keg Cop - Daisy Chain RJ45 T with Slots.sch, Keg Cop - Daisy Chain T with Slots.brd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]
2019-12-30 Add in flow handling and config
2019-12-31 Work on not missing flow points
    [kegflow.cpp, main.cpp]
2019-12-31 Fix memory size for JSON
    [main.cpp]
2020-01-01 Swap pins, split dirs
    [Keg Cop - Daisy Chain RJ45 T with Slots.brd, Keg Cop - Daisy Chain RJ45 T with Slots.sch, Keg Cop - Daisy Chain T with Slots.brd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]
2020-01-05 Renamed files
    [Keg Cop - Pinout.brd, Keg Cop - RJ45 - 6-Pack Tallboy.brd, Keg Cop - RJ45 - 6-Pack Tallboy.sch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]
2020-01-05 New boards
    [Keg Cop - Eight Straight.brd, Keg Cop - Eight Straight.sch, Keg Cop - Pinout.sch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]
2020-01-05 Refactor mDNS and reboot timers
    [main.cpp]
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2020-01-12 Renamed and updated images to follow
    [Keg Cop - Daisy Chain RJ45 T with Slots.brd, Keg Cop - Daisy Chain RJ45 T with Slots.sch]
2020-01-12 Re-work pour
    [Keg Cop - Eight Straight.brd]
2020-01-12 No longer needed
    [Keg Cop - Pinout.brd, Keg Cop - Pinout.sch]
2020-01-12 Rename files
    [Keg Cop - 6-Pack.brd, Keg Cop - 6-Pack.sch, Keg Cop - Daisy Chain.brd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]
2020-01-26 Updates to names and traces
2020-04-19 Add dasy-chain cases
    [DaisyChainCase_1.stl, DaisyChainCase_2.stl, DaisyChainCase_3.stl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]
2020-04-19 Add RPints compatability framework
2020-04-19 Update to new config framework
2020-04-19 Update to new wifi framework
2020-04-19 Switch libraries to private repos
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2020-04-19 Fix selective preprocessor directives
    [ntp.cpp]
2020-04-21 Fix carriage return in debug
2020-04-24 Move temp calibration to array to assist tempsensors struct
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2020-04-25 Move thermostat to millis() (no change to compile issue)
    [config.h, thermostat.cpp]
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2020-04-27 Get rid of begin(): bind error: -8
    [main.cpp]
2020-05-02 Redesign page flow
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2020-05-13 New Devel board
    [Keg Cop - Devel.brd, Keg Cop - Devel.sch]
2020-05-13 Add proper value for R6
    [Keg Cop - Devel.brd, Keg Cop - Devel.sch]
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2020-05-13 Change KEGx pins to FLOWx, generate default doc
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2020-05-15 Allow loading of config before serial, dummy mode on failure
    [config.h, main.cpp]
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2020-05-18 Fix relays flickering at startup
    [main.cpp]
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2020-05-19 Clarify wifi reset flow
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2020-05-20 Rename and add config demo JSON
    [Demo Config JSON.txt]
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2020-05-25 Fix thermostat logic, update debug
    [thermostat.cpp]
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2020-05-31 Add DS18B20 sensor
    [Keg Cop - Tallboy.brd, Keg Cop - Tallboy.sch]
2020-05-31 Update images
    [Keg Cop.brd]
2020-06-02 Begin new board for 8 flowmeters
    [Keg Cop - New 8-Pack.brd, Keg Cop - New 8-Pack.sch]
2020-06-02 New sensor board
    [Keg Cop - Sensors.brd, Keg Cop - Sensors.sch]
2020-06-02 Fix silkscreen
    [Keg Cop - 6-Pack.brd]
2020-06-02 Add silkscreen to back of daisy chain board
    [Keg Cop - Daisy Chain.brd]
2020-06-02 Tweak silkscreen
    [Keg Cop - Daisy Chain.brd]
2020-06-06 Shorten switch in settings/tapnum
2020-06-06 Get rid of getJSON errors when switching pages
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2020-06-14 Organize files
    [Keg Cop - 6-Pack.brd, Keg Cop - 6-Pack.sch, Keg Cop - Daisy Chain.brd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]
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2020-07-05 Donnie updated the cases
    [DaisyChainCase_1.stl, DaisyChainCase_2.stl, DaisyChainCase_3.stl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]
2020-07-05 Add debug to catch bit flip
    [main.cpp]
2020-07-06 Fix flow logging
2020-07-07 Add separate power for sol/cool
    [Keg Cop - Devel.brd, Keg Cop - Devel.sch]
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2020-07-07 Increment version on silkscreen
    [Keg Cop - Devel.brd]
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2020-07-12 Fix a couple links
2020-07-17 Fix 404 on #sensorcontrol post
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2020-08-23 New case
    [Sensor Board Enclosure - Bottom.stl, Sensor Board Enclosure - Top.stl]
2020-09-05 Add Tallboy case
    [TallBoy Enclosure - Bottom.stl, TallBoy Enclosure - Top.stl]
2020-09-05 New board
    [NAU7802.brd, NAU7802.sch]
2020-09-07 Rewire, move to 9 meters
    [Keg Cop - 8-Pack.brd, Keg Cop - 8-Pack.sch, Keg Cop - Daisy Chain.brd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]
2020-10-11 Move scale to new directory
    [NAU7802.brd, NAU7802.sch, scale.brd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]
2020-10-12 Updated board with second tab
    [Main Enclosure - Bottom.stl, Main Enclosure - Top.stl]
2020-10-14 Minor changes and cleanup
    [scale.brd, scale.sch]
2020-10-14 Shorten heap debug message
    [serialhandler.cpp]
2020-10-17 Add pullups, move KEG0 to GPIO13
    [Keg Cop - Main.brd, Keg Cop - Main.sch]
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2020-10-17 Brand board
    [Keg Cop - Daisy Chain.brd]
2020-10-17 Brand boards
    [Keg Cop - Sensors.brd]
2020-10-17 Deleted unused files
    [Keg Cop - Eight Straight.brd, Keg Cop - Eight Straight.sch, RJ45 - Breakout.brd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]
2020-10-17 Modify for pcbs.io type of conversion
    [Keg Cop - Daisy Chain.brd, Keg Cop - Main.brd, Keg Cop - Sensors.brd]
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2020-10-18 Add reset reason to handler
    [serialhandler.cpp]
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2020-11-04 K0 to 4 K1 to 16 SOL to 2
    [Keg Cop - Main.brd, Keg Cop - Main.sch]
2020-11-05 Add series resistor
    [Keg Cop - Daisy Chain.brd, Keg Cop - Daisy Chain.sch]
2020-11-05 Add scale terminal
    [scale.brd, scale.sch]
2020-11-16 Updated Daisy Chain
    [Keg Cop - Daisy Chain.brd, Keg Cop - Daisy Chain.sch]
2020-12-09 Use 32 for wifi reset
    [config.h]
2020-12-11 Add discrete reset reasons
    [serialhandler.cpp]
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2021-03-01 Add meter breakout
    [Keg Cop - Meter Breakout.brd, Keg Cop - Meter Breakout.sch]
2021-03-01 Add ground pour vias
    [Keg Cop - Meter Breakout.brd]
2021-03-03 Add keg scale board
    [keg-scale.brd, keg-scale.sch]
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2021-03-08 Further fix resetinfo for ESP8266
    [serialhandler.cpp]
2021-03-08 Fix SPIFFS include for ESP32
2021-03-09 Fix ArduinoJson errors
2021-03-14 Add molex daisychain board
    [Keg Cop - Daisy Chain Molex.brd, Keg Cop - Daisy Chain Molex.sch]
2021-03-17 Reorganize daisy chain boards
    [Keg Cop - Daisy Chain Molex.brd, Keg Cop - Daisy Chain Molex.sch, Keg Cop - Daisy Chain Screw.brd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]
2021-03-20 Remove ESP8266 work
    [keg-scale.brd, keg-scale.sch]
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2021-03-26 Fix MQTT timer
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2021-03-27 Add 24 hour reboot timer
    [main.cpp]
2021-04-01 Update docs
    [Keg Cop - Parts.csv, Keg Cop - Values.csv]
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2022-07-09 Promote Devel to 1.1.0 (#39)
    * Add taplistioTap to Taps struct
    * Add config for taplistio tap number, fix tap label
    * Add taplistio venue/secret handling
    * Send pours to Taplist.io
    * Add documentation for taplist.io support
    * Fix docs for #8
    * Fix #8 (again)
    * Fix for #10
    * Skip taplistio send if taplistio tap ID is 0
    Fixes #18
    * Update for #19
    * Update Copyright date
    * Ignore DS_Store on Mac
    * Update Alpha firmware
    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
    [partitions.csv]
2022-08-12 Devel (#94)
    * Clean JavaScript (#54)
    * Use js for each page
    * Add common js file
    * Move on page load events to common file
    * Moves temp page visible to common
    * Moves loader to common
    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
    [Keg Cop - 6-way Breakout.kicad_pcb, Keg Cop - 6-way Breakout.kicad_sch, Keg Cop - Devel SMD.brd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]
2022-08-21 Feature 86 (#104)
    * Add load spinner div to each page
    * Add load spinner stub to each page
    * Move alerts to common
    * Cleanup load/unload
    * Move flowcal
    * Move pollComplete() to common
    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
2022-08-21 New graphics (#105)
    * Split common JS for jQuery
    * Allow setting a dev server (#55)
    * Add load spinner stub to each pag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
2022-08-22 Add tower fan thermostat (#107)
    * Add load spinner stub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
2022-08-24 Debug links (#108)
    * Missing brace
    * Remove duplicate function
    * Be sure to null out dataHost
    [thermostat.cpp]
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2022-08-29 Swap theme (#119)
    * Add basis for changing theme
    * Re-write page on theme switch
    * Update Bootswatch
    * Expand CSS per theme
    * Re-do context help alignment (BS 5.x)
    * Re-align temp/control box
    * Fix card header/button alignment
    * Restore loader
    * Move ota to settings
    * Fix spacing on forms
    * Move themes to an array of objects
    * Add basic UI to select theme
    * Update UI selection screen
2022-09-03 Bad update flag (#126)
    * Add bad update flag to model
    * Add bad update notice to UI
    * Skip FS update on bad FW update
    * Add getTime() function
    * Add bad update flag to config
    * Add bad update flags to thisVersion
    * Flag bad updates
    [main.cpp]
2022-09-09 Bulk load (#131)
    * Add gettheme so we can set without settings.htm
    * Add getTheme() to set themese on all pages
    * Add json merge capability
    * Add /bulkload/ route
    * Add base pages
    * Rename config files
    * Split out config handling
    * Split out common json tools
    * Add bulk handler
    * Rename config object to app
    * Use functions across files
    * Rename config files
    * Reduce string duplication
    * Reduce data copy in config load
    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
    [appconfig.cpp, config.h]
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2022-09-12 Kstv json (#137)
    * Add kstv.json
    * Update KSTV keys
    * Cleanup debug (#136)
    * Add kstv.json
    * Update KSTV keys
    * Remove debug condition on Telnet
    * Remove debug condition on /edit
    * Add kstv.json
    * Remove needless keys, move KS-TV
    * Make keys public, add functions for KS-TV
    * Call KS-TV setup
    * Fix a couple mistakes
    * Use ststic key names
    [config.h, main.cpp, serialhandler.cpp]
2022-09-18 Filesystem stability (#139)
    * Don't need string
    * Change to 5.0 class for SR-only
    * Move semaphore earlier
    * Move reconnect out of callback
    * Clean up filesystem logic
    [main.cpp]
2023-07-19 Feature Release 1.3.0 (#202)
    * Remove kegscreen service advertisement
    * Fix mDNS keys
    * Fix for #146
    * Use proper div
    * Add scanNetworks() to reconnect
    * Go back to platform package 1.0.6
    * Stub this in for later
    * Explicit python decl
    * Add post process to zip data files
    * Add .gz handler
    * Update uptime refresh
    * Update proper version.json
    * Change partition setup
    * Fix active links
    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
    [ota.csv, partitions.csv]

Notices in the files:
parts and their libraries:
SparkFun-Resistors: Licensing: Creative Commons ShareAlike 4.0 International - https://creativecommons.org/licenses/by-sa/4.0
